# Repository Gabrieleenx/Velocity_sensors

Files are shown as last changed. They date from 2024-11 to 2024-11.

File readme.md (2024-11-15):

# Velocity sensor 

This is a build guide for the velocity sensor used in the paper "Perception, Control and Hardware for In-Hand Slip-Aware Object Manipulation with Parallel Grippers", preprint available at: https://arxiv.org/abs/2410.19660. Everything is provided as is. 

The main repo for that project can be found at https://github.com/Gabrieleenx/Slip-Aware-Object-Manipulation-with-Parallel-Grippers 

This readme contains the following:
* Overview
* Overview of code
* Parts list
* Build guide

## Overview 

This repo is about the velocity sensors that are mounted on the figers of the gripper described in https://github.com/Gabrieleenx/Slip-Aware-Object-Manipulation-with-Parallel-Grippers. I have plans to redesign these sensors, the current version funciton and does what they where built to do, but there are some properties I would like to improve. The sensors can be seen bellow:

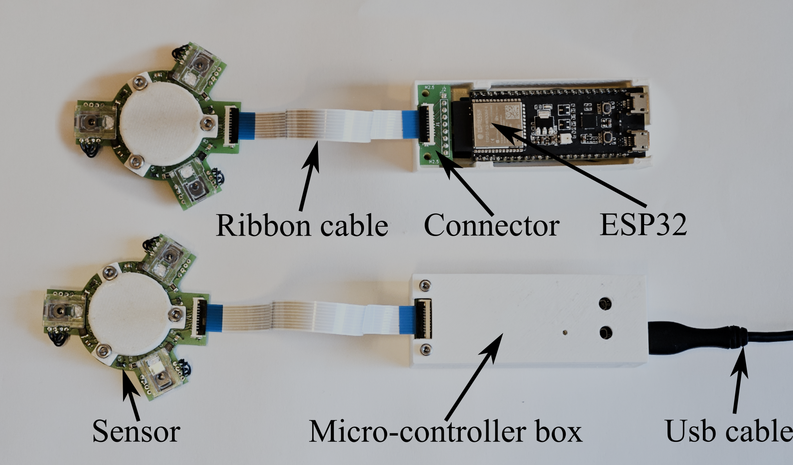
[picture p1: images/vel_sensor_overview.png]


These senors are mounted on the gripper like following:

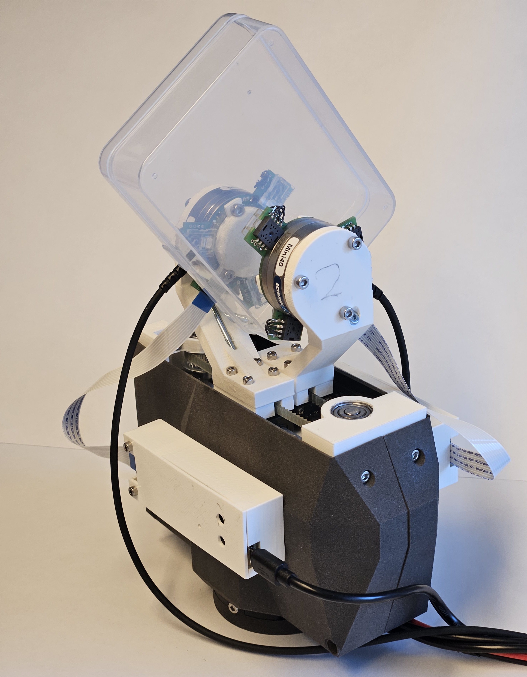
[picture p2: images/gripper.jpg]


The sensor can meassure velocity in x, y and rotation for a flat surface sliding in the gripper. Currently I have the sensor output velocity measurements at 120 Hz. And they have simple outlier rejection, where if one sensor is outside of the object, the tracking still functions. 

## Overview of code

The code can be found in the folder /code. The code is compiled using platfromIO, see the platformio.ini for the settings. 

One important thing is to set the "sensor_name = "sensor_2";" variable on line 16 in main.cpp, to either "sensor_1" or "sensor_2" depending on which finger it goes on, you can make up your own names aswell. 

The code to communicate with the sensors can be found at  https://github.com/Gabrieleenx/Slip-Aware-Object-Manipulation-with-Parallel-Grippers.

The code uses freeRTOS, built into the Arduio framework, one core is tasked with bitbanging the sensors and the other is doing filtering and serial communication. Here we use the ESP32-S3-DEVKITC-1-N8R2, whcih has the UART to USB, in comparion to the gripper, https://github.com/Gabrieleenx/Parallel_gripper. 

## Parts list

This part list is for one sensor:

1x ESP32-S3-DEVKITC-1-N8R2 https://www.digikey.se/sv/products/detail/espressif-systems/ESP32-S3-DEVKITC-1-N8R2/15199627?productid=15199627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

3x rapoo m300 (we will take the chip, lens and LED) https://www.rapoo-eu.com/product/m300-silent/

3x 50 ohm resisor https://se.rs-online.com/web/p/surface-mount-resistors/2430511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

1x hrough Hole Pin Header https://se.rs-online.com/web/p/pcb-headers/7671025?searchId=941cb68f-9620-4753-9d9d-7a9d76368953&gb=s

2x Molex, Easy-On, 200528 1mm Pitch 9, https://se.rs-online.com/web/p/fpc-connectors/1213341?searchId=74c22de1-7fd5-41bc-b195-446cd1a22052&gb=s

1x FFC Ribbon Cable, 9-Way, 1mm Pitch, 152mm, https://se.rs-online.com/web/p/ribbon-cable/1222519?searchId=01f7c47b-5acd-4eca-bbf9-52f6bdeb05a2&gb=s 

3x 10μF Tantalum Capacitor 16V dc, https://se.rs-online.com/web/p/tantalum-capacitors/1882267?searchId=6749729e-8b06-4c40-b989-853f3fd36829&gb=s

3x 1μF Tantalum Capacitor 16V dc, https://se.rs-online.com/web/p/tantalum-capacitors/1882297?searchId=ff8f216c-4b23-46ba-a96b-6da0473a7bb6&gb=s

3x 100nF Multilayer Ceramic Capacitor MLCC, https://se.rs-online.com/web/p/mlccs-multilayer-ceramic-capacitors/2644416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

1x USB cable, with micro usb

dupont cables

2x m2.5 20mm screw and nut to mount the lid

2x m2.5 srew and nut to mount the microcontroller box, length depends on

3x m3 screw, to mount the sensor, length depends on

## PCB boards
* Sensor board 2 layer, see gerber files (traces have been updated, jumper wires no longer needed)
* Connector board 2 layer, see gerber files 

## 3D print

The controleller box is printed in 2 pices, bottom and top, both in PLA. The contact pad stl can be found at https://github.com/Gabrieleenx/Parallel_gripper. Otherwise see stl_files.

## Build guide

See below for how to solder on the componenets or chech the gerberfiles. The same pattern follows for all 3 sensors. 

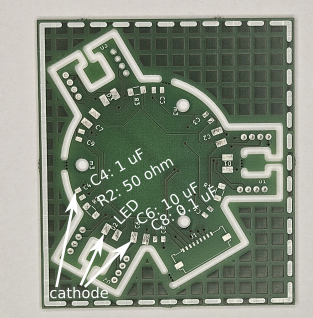
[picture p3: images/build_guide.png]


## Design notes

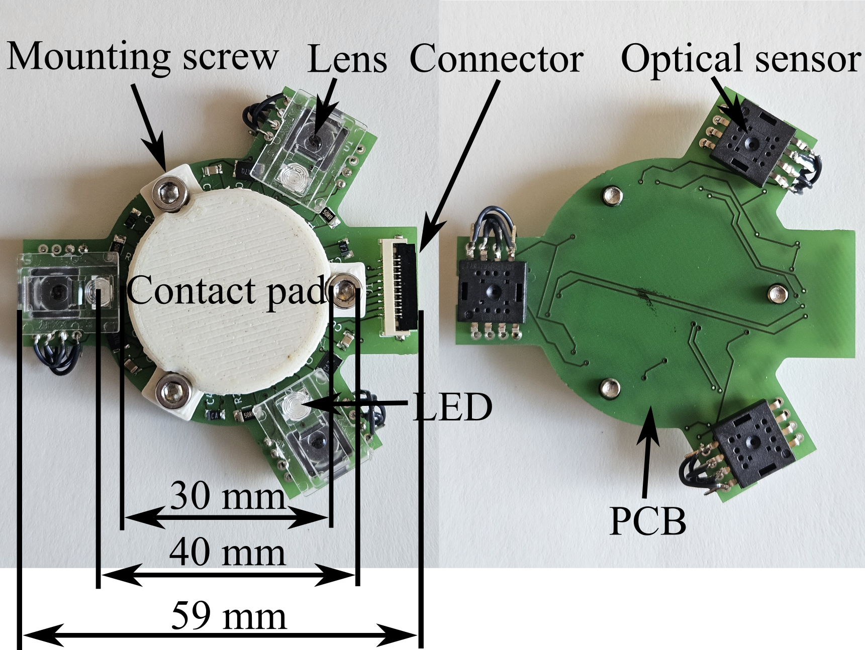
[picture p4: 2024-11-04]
images/vel_sensors.png

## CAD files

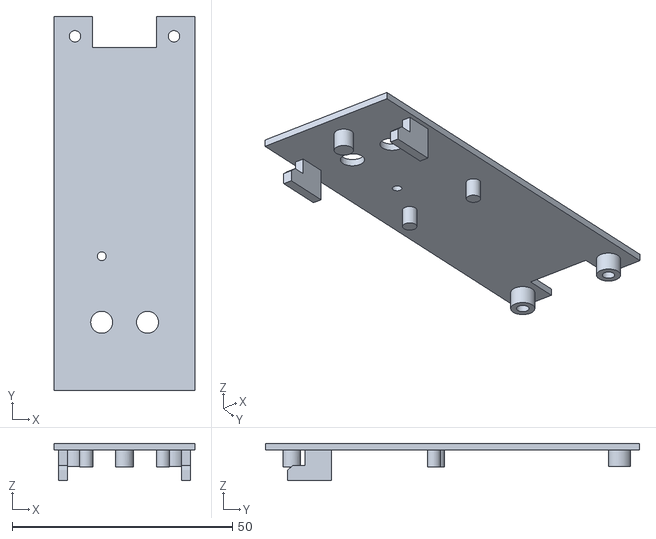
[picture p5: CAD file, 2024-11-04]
stl_files/Hull_top.stl
32.0 x 85.0 x 8.50

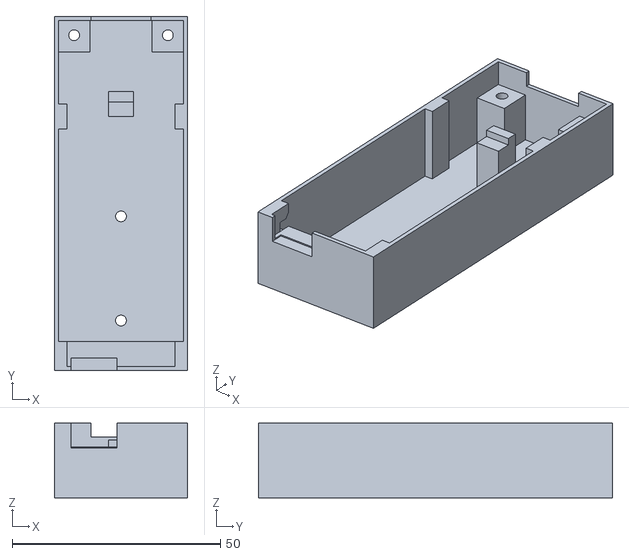
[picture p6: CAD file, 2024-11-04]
stl_files/Hull_bottom.stl
32.0 x 85.0 x 18.0

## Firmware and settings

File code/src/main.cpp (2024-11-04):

#include <Arduino.h>
#include "esp_task_wdt.h"
#include "FreeRTOS.h"
#include "task.h"
#include <EEPROM.h>
#include "filter_utils.h"
const int data_pin_sensor_1 = 4;
const int clk_pin_sensor_1 = 5;

const int data_pin_sensor_2 = 6;
const int clk_pin_sensor_2 = 7;

const int data_pin_sensor_3 = 15;
const int clk_pin_sensor_3 = 16;

const String sensor_name = "sensor_2";

int counts_per_inch = 3200; // should be 1600, but measurements say otherwise. sensor resulution.

const double d = 0.026; // [m] from center to sensor. 

int correct_prod_id1 = 0x31; // ID of sensor 

int individual_sensor = 0;

const uint8_t sensor_reg_dx = 0x03; // 0x03
const uint8_t sensor_reg_dy = 0x04; // 0x04
const uint8_t sensor_reg_motion = 0x02;
const uint8_t sensor_reg_PId1 =0x00;
unsigned long lastTimeMicros_;

const double tracking_loop_Kp = 40;
const double tracking_loop_Ki = 500;

bool connected_sensor_1 = 0;
bool connected_sensor_2 = 0;
bool connected_sensor_3 = 0;

// FreeRTOS handles for the tasks and mutex
TaskHandle_t sensorTaskHandle;
TaskHandle_t serialTaskHandle;
SemaphoreHandle_t mutex;

// Global data storage


SensorDataDelta sensor_1_delta = {0, 0};
SensorDataDelta sensor_2_delta = {0, 0};
SensorDataDelta sensor_3_delta = {0, 0};

// Useful functions

void setAllDataInput(){
  pinMode (data_pin_sensor_1, INPUT); 
  pinMode (data_pin_sensor_2, INPUT); 
  pinMode (data_pin_sensor_3, INPUT); 
}

void setAllDataOutput(){
  pinMode (data_pin_sensor_1, OUTPUT); 
  pinMode (data_pin_sensor_2, OUTPUT); 
  pinMode (data_pin_sensor_3, OUTPUT); 
}


void setAllClkOutput(){
  pinMode (clk_pin_sensor_1, OUTPUT); 
  pinMode (clk_pin_sensor_2, OUTPUT); 
  pinMode (clk_pin_sensor_3, OUTPUT); 
}

void digitalWriteDataAll(int w){
 
  digitalWrite(data_pin_sensor_3, w);
  digitalWrite(data_pin_sensor_2, w);
  digitalWrite(data_pin_sensor_1, w);
          
}

void digitalWriteClkAll(int w){
  digitalWrite(clk_pin_sensor_1, w);
  digitalWrite(clk_pin_sensor_3, w); 
  digitalWrite(clk_pin_sensor_2, w);  
}



void sensorWriteReg(uint8_t address, uint8_t data){
  // Set MSB high
  address |= 0x80;
  setAllDataOutput();
  int t_hold = 5;
  for (int i=7; i>=0; i--){
    digitalWriteClkAll(LOW);
    digitalWriteDataAll(address & (1 << i));
    delayMicroseconds(t_hold);
    digitalWriteClkAll(HIGH);
    delayMicroseconds(t_hold);
  }
  for (int i=7; i>=0; i--){
    digitalWriteClkAll(LOW);
    digitalWriteDataAll(data & (1 << i));
    delayMicroseconds(t_hold);
    digitalWriteClkAll(HIGH);
    delayMicroseconds(t_hold);
  }
}

void sensorReadReg(const uint8_t address, int* r){
  setAllDataOutput();
  int t_hold = 5;

  for (int i=7; i>=0; i--){
    digitalWriteClkAll(LOW);
    digitalWriteDataAll(address & (1 << i));
    delayMicroseconds(t_hold);
    digitalWriteClkAll(HIGH);
    delayMicroseconds(t_hold);
  }

  digitalWriteDataAll(LOW); 
  delayMicroseconds(2);
  setAllDataInput();
  delayMicroseconds(2);
  
  for (int i=7; i>=0; i--){        
    digitalWriteClkAll(LOW);
    delayMicroseconds(t_hold);
    digitalWriteClkAll(HIGH);
    delayMicroseconds(t_hold);
    
    r[2] |= (digitalRead(data_pin_sensor_3) << i);
    r[1] |= (digitalRead(data_pin_sensor_2) << i);
    r[0] |= (digitalRead(data_pin_sensor_1) << i);
    
  }

}


void reSynchSensor(){
  // This assumes same procedure as PAW3204 
  setAllDataOutput();
  digitalWriteDataAll(LOW);
  setAllDataInput(); // set in HI-Z
  digitalWriteClkAll(HIGH);
  delayMicroseconds(5);
  digitalWriteClkAll(LOW); 
  delayMicroseconds(2);
  digitalWriteClkAll(HIGH); 
  delay(5); // t_siwtt, timeout watchdog 1.7 ms
  sensorWriteReg(0x85, 0x21); // reg: 85 data: 0x21   00100001 write operation mode    force wake up with disabled sleep
  sensorWriteReg(0x86, 0x06); // 86 06   write configuration      CPI 1600  // 00000110
}


void getProdID(signed char* prod_id){
  int r[3] = {0,0,0};
  sensorReadReg(sensor_reg_PId1, r);
  prod_id[0] = (signed char) r[0];
  prod_id[1] = (signed char) r[1];
  prod_id[2] = (signed char) r[2];
}


void sensorDx(signed char* dx){
  int r[3] = {0,0,0};
  sensorReadReg(sensor_reg_dx, r);
  dx[0] = (signed char) r[0];
  dx[1] = (signed char) r[1];
  dx[2] = (signed char) r[2];
} 

void sensorDy(signed char* dy){
  int r[3] = {0,0,0};
  sensorReadReg(sensor_reg_dy, r);
  dy[0] = (signed char) r[0];
  dy[1] = (signed char) r[1];
  dy[2] = (signed char) r[2];
} 

int extractBit7(int value) {
  return (value >> 7) & 1;
}

void sensorMotion(int* motion){
  int r[3] = {0,0,0};
  sensorReadReg(sensor_reg_motion, r);
  motion[0] = extractBit7(r[0]);
  motion[1] = extractBit7(r[1]);  
  motion[2] = extractBit7(r[2]);
}

void setSensorSettings(){
  // set up 3 sensors
  int i = 0;
  signed char sensor_prod_id[] = {0,0,0};

  while(i < 100){
    reSynchSensor();
    getProdID(sensor_prod_id);
    if (sensor_prod_id[0] == correct_prod_id1){
      connected_sensor_1 = 1;
    }
    else{
      Serial.print("Chip 1 prodid");
      Serial.println(sensor_prod_id[0]);   
    }
    if (sensor_prod_id[1] == correct_prod_id1){
      connected_sensor_2 = 1;
    }
    else{
      Serial.print("Chip 2 prodid");
      Serial.println(sensor_prod_id[1]);   
    }
    if (sensor_prod_id[2] == correct_prod_id1){
      connected_sensor_3 = 1;
    }    else{
      Serial.print("Chip 3 prodid");
      Serial.println(sensor_prod_id[2]);   
    }

    if (connected_sensor_1 == 1 && connected_sensor_2 == 1 && connected_sensor_3 == 1){
      break;
    }
    i++;
    delay(1);
  }
  sensorWriteReg(0x85, 0x21); // reg: 85 data: 0x21   00100001 write operation mode    force wake up with disabled sleep
  sensorWriteReg(0x86, 0x86); // chip reset 
  delayMicroseconds(3); 
  sensorWriteReg(0x85, 0x21); // reg: 85 data: 0x21   00100001 write operation mode    force wake up with disabled sleep
  sensorWriteReg(0x86, 0x06); // 86 06   write configuration      CPI 1600  // 00000110
}

void readSerial(String& msg, FilterSensorData &sensor_filter){
  while (Serial.available()) {
    // get the new byte:
    char ch = Serial.read();
    msg += ch;
    // end of user input
    if (ch == '\n') {
      if (msg[0] == 'n'){
      // send name of sensor 
      Serial.print("n");
      Serial.print("/t");
      Serial.println(sensor_name); 
      }
      if (msg[0] == 'c'){
        individual_sensor = msg[1] - '0';
      }
      if (msg[0] == 'k'){
        /* 
        cal_nr = {0,x: radious, 1,0: s_1_x_a, 1,1: s_1_x_b,
                  1,2: s_1_y_a, 1,3: s_1_y_b,
                  2,0: s_2_x_a, 2,1: s_2_x_b,
                  2,2: s_2_y_a, 2,3: s_2_y_b,
                  3,0: s_3_x_a, 3,1: s_3_x_b,
                  3,2: s_3_y_a, 3,3: s_3_y_b,}
        */
        int cal_nr_1 = msg[1] - '0';
        int cal_nr_2 = msg[2] - '0';
        String substr = msg.substring(3);

        double value = substr.toDouble();
        sensor_filter.update_calibration(cal_nr_1, cal_nr_2, value);
      }
      msg = "";
      return;
    }
  }
}



void sensorUpdate(){
  signed char dx[] = {0,0,0};
  signed char dy[] = {0,0,0};
  int motion[] = {0,0,0};

  // check that sensor is in sync by reading the sensor id
  signed char sensor_prod_id[] = {0,0,0};
  getProdID(sensor_prod_id);
  if (sensor_prod_id[0] == correct_prod_id1 && sensor_prod_id[1] == correct_prod_id1 && sensor_prod_id[2] == correct_prod_id1){
    
    sensorMotion(motion);

    sensorDy(dy);
    sensorDx(dx);
    if( xSemaphoreTake( mutex, ( TickType_t ) 10 ) == pdTRUE ){
      sensor_1_delta.dx += (int) dx[0];
      sensor_1_delta.dy += (int) dy[0];

      sensor_2_delta.dx += (int) dx[1];
      sensor_2_delta.dy += (int) dy[1];

      sensor_3_delta.dx += (int) dx[2];
      sensor_3_delta.dy += (int) dy[2];
      xSemaphoreGive( mutex );
    }
    vTaskDelay(1);

  }
  else{
    Serial.print("n");
    Serial.print("/t");
    Serial.println("resynch");
    Serial.print(sensor_prod_id[0]);
    Serial.print(" ");
    Serial.print(sensor_prod_id[1]);
    Serial.print(" ");
    Serial.println(sensor_prod_id[2]);
    reSynchSensor();
    return;
  }
}


void sensorLoop(void *pvParameters) {
  setSensorSettings();
  while (true) {
    sensorUpdate();
  }
}


void serialTask(void *pvParameters) {
  SensorDataDelta sensor_1_delta_copy = {0, 0};
  SensorDataDelta sensor_2_delta_copy = {0, 0};
  SensorDataDelta sensor_3_delta_copy = {0, 0};
  FilterSensorData sensor_filter(80, 300, counts_per_inch);
  String msg = "";
  while (true) {

    if( xSemaphoreTake( mutex, ( TickType_t ) 10 ) == pdTRUE ){
      sensor_1_delta_copy = sensor_1_delta;
      sensor_1_delta.reset();
      sensor_2_delta_copy = sensor_2_delta;
      sensor_2_delta.reset();
      sensor_3_delta_copy = sensor_3_delta;
      sensor_3_delta.reset();
      xSemaphoreGive( mutex );
    }
    if (individual_sensor == 0){
      sensor_filter.update(sensor_1_delta_copy, sensor_2_delta_copy, sensor_3_delta_copy);
      Serial.print("v");
      Serial.print("/t");
      Serial.print(sensor_filter.get_vx(), 4);
      Serial.print("/t");
      Serial.print(sensor_filter.get_vy(), 4);
      Serial.print("/t");
      Serial.println(sensor_filter.get_omega(), 4);
    }
    else{
      unsigned long currentTimeMicros = micros(); 
      // Overflows after 71.58 min
      if (currentTimeMicros < lastTimeMicros_){
        lastTimeMicros_ = currentTimeMicros;
      }
      double dt =  ((double)(currentTimeMicros - lastTimeMicros_))/1e6; 
      lastTimeMicros_ = currentTimeMicros;
      double vx = 0.0;
      double vy = 0.0;
      double omega = 0.0;
      if (individual_sensor == 1){
        vx = dxToMilimeter(sensor_1_delta_copy.dx, counts_per_inch)/dt;
        vy = dxToMilimeter(sensor_1_delta_copy.dy, counts_per_inch)/dt;
      }
      if (individual_sensor == 2){
        vx = dxToMilimeter(sensor_2_delta_copy.dx, counts_per_inch)/dt;
        vy = dxToMilimeter(sensor_2_delta_copy.dy, counts_per_inch)/dt;
      }
      if (individual_sensor == 3){
        vx = dxToMilimeter(sensor_3_delta_copy.dx, counts_per_inch)/dt;
        vy = dxToMilimeter(sensor_3_delta_copy.dy, counts_per_inch)/dt;
      }


      Serial.print("v");
      Serial.print("/t");
      Serial.print(vx, 4);
      Serial.print("/t");
      Serial.print(vy, 4);
      Serial.print("/t");
      Serial.println(sensor_filter.get_omega(), 4);

    }
   
    readSerial(msg, sensor_filter);
    vTaskDelay(6);
  }
}


void setup() {
  Serial.begin(115200);
  //Serial.println("Serial start");
  mutex = xSemaphoreCreateMutex();

  delay(10);

  // set pins 
  setAllClkOutput();
  setAllDataInput();

  //Serial.println("Begin setup");
  delay(1000);
  //Serial.println("Setup done");

  xTaskCreatePinnedToCore(
    sensorLoop,       // Task function
    "SensorTask",     // Name of the task
    2048,               // Stack size (bytes)
    NULL,               // Parameter to pass
    1,                  // Task priority
    &sensorTaskHandle,// Task handle
    0                   // Core to pin the task to (0 or 1)
  );
  
  xTaskCreatePinnedToCore(
    serialTask,       // Task function
    "SerialTask",     // Name of the task
    2048,               // Stack size (bytes)
    NULL,               // Parameter to pass
    1,                  // Task priority
    &serialTaskHandle, // Task handle
    1                   // Core to pin the task to (0 or 1)
  );
}

void loop() { 
// Do nothing 
}

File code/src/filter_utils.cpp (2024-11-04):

#include <Arduino.h>
#include "filter_utils.h"

double dxToMilimeter(int dx, int countsPerInch){
  double countsPerMilimeter = (double) countsPerInch / 25.4;
  double dx_mm = (double) dx/countsPerMilimeter;
  return dx_mm;
}


TargetTrackingLoopFilter::TargetTrackingLoopFilter(double kp_, double ki_, int countsPerInch_){
  //https://www.embeddedrelated.com/showarticle/530.php
  lastTimeMicros = micros();
  pos = 0.0;
  pos_est = 0.0;
  vel_est = 0.0;
  vel_int = 0.0;
  kp = kp_;
  ki = ki_;
  countsPerInch = countsPerInch_;
}

double TargetTrackingLoopFilter::update(int dx){
  // TOOD add calibration here 
  
  pos += dxToMilimeter(dx, countsPerInch);
  unsigned long currentTimeMicros = micros(); 
  // Overflows after 71.58 min
  if (currentTimeMicros < lastTimeMicros){
    lastTimeMicros = currentTimeMicros;
  }
  double dt =  ((double)(currentTimeMicros - lastTimeMicros))/1e6; 
  lastTimeMicros = currentTimeMicros;
  
  pos_est += vel_est*dt;
  double pos_error = pos - pos_est;
  vel_int += pos_error * ki * dt; 
  vel_est = pos_error*kp + vel_int;
  
  double vel_est_ = dxToMilimeter(dx, countsPerInch)/dt;
  return vel_est_;
}

VelocityFilter::VelocityFilter(double a_, double b_, int countsPerInch_){
  lastTimeMicros = micros();
  countsPerInch = countsPerInch_;
  a = a_;
  b = b_;
}

double VelocityFilter::update(int dx){
  unsigned long currentTimeMicros = micros(); 
  // Overflows after 71.58 min
  if (currentTimeMicros < lastTimeMicros){
    lastTimeMicros = currentTimeMicros;
  }
  double dt =  ((double)(currentTimeMicros - lastTimeMicros))/1e6; 
  lastTimeMicros = currentTimeMicros;

  double vel_est_ = dxToMilimeter(dx, countsPerInch)/dt;
  double cal_vel_est = vel_est_/(b + a*vel_est_);
  return cal_vel_est;
}


FilterSensorData::FilterSensorData(double kp_, double ki_, int countsPerInch_)
    : ttlf_dx_1(0.0, 1.0, countsPerInch_),
      ttlf_dy_1(0.0, 1.0, countsPerInch_),
      ttlf_dx_2(0.0, 1.0, countsPerInch_),
      ttlf_dy_2(0.0, 1.0, countsPerInch_),
      ttlf_dx_3(0.0, 1.0, countsPerInch_),
      ttlf_dy_3(0.0, 1.0, countsPerInch_) {
  d_Sensor = 20.3; // [mm] from center to sensor. 
}

void FilterSensorData::update_calibration(int cal_nr_1, int cal_nr_2, double value){
  if (cal_nr_1 == 0){
    d_Sensor = value;
    Serial.print("radius is updated to: ");
    Serial.println(d_Sensor);
    return;
  }
  if (cal_nr_1 == 1){
    if (cal_nr_2 == 0) {
      ttlf_dx_1.update_a(value);
      return;
    }
    if (cal_nr_2 == 1) {
      ttlf_dx_1.update_b(value);
      return;
    }
    if (cal_nr_2 == 2) {
      ttlf_dy_1.update_a(value);
      return;
    }
    if (cal_nr_2 == 3) {
      ttlf_dy_1.update_b(value);
      return;
    }
  }

  if (cal_nr_1 == 2){
    if (cal_nr_2 == 0) {
      ttlf_dx_2.update_a(value);
      return;
    }
    if (cal_nr_2 == 1) {
      ttlf_dx_2.update_b(value);
      return;
    }
    if (cal_nr_2 == 2) {
      ttlf_dy_2.update_a(value);
      return;
    }
    if (cal_nr_2 == 3) {
      ttlf_dy_2.update_b(value);
      return;
    }
  }

  if (cal_nr_1 == 3){
    if (cal_nr_2 == 0) {
      ttlf_dx_3.update_a(value);
      return;
    }
    if (cal_nr_2 == 1) {
      ttlf_dx_3.update_b(value);
      return;
    }
    if (cal_nr_2 == 2) {
      ttlf_dy_3.update_a(value);
      return;
    }
    if (cal_nr_2 == 3) {
      ttlf_dy_3.update_b(value);
      return;
    }
  }


}



void FilterSensorData::update(SensorDataDelta sensor_1, 
                              SensorDataDelta sensor_2, 
                              SensorDataDelta sensor_3){
  // Velocity tracking loop
  double vx_1 = ttlf_dx_1.update(sensor_1.dx);
  double vy_1 = ttlf_dy_1.update(sensor_1.dy);

  double vx_2 = ttlf_dx_2.update(sensor_2.dx);
  double vy_2 = ttlf_dy_2.update(sensor_2.dy);

  double vx_3 = ttlf_dx_3.update(sensor_3.dx);
  double vy_3 = ttlf_dy_3.update(sensor_3.dy);


  vx = sqrt(3.0)/6.0 * vx_1 - 1.0/6.0 * vy_1 - sqrt(3.0)/6.0 * vx_2 - 1.0/6.0 * vy_2 + 1.0/3.0 * vy_3;
  vy = -1.0/6.0 * vx_1 - sqrt(3.0)/6.0 * vy_1 - 1.0/6.0 * vx_2 + sqrt(3.0)/6.0 * vy_2 + 1.0/3.0 * vx_3;
  omega = 1.0/(3.0*d_Sensor) * (vx_1 + vx_2 + vx_3);

  // calculate error for each sensor 
  double vx_1_hat = cos(PI/6)*vx - sin(PI/6)*vy + d_Sensor*omega;
  double vy_1_hat = -sin(PI/6)*vx - cos(PI/6)*vy;
  double vx_2_hat = -cos(-PI/6)*vx + sin(-PI/6)*vy + d_Sensor*omega;
  double vy_2_hat = sin(-PI/6)*vx + cos(-PI/6)*vy;
  double vx_3_hat = vy + d_Sensor*omega;
  double vy_3_hat = vx;

  double e_1 = sqrt(pow(vx_1-vx_1_hat, 2) + pow(vy_1-vy_1_hat, 2));
  double e_2 = sqrt(pow(vx_2-vx_2_hat, 2) + pow(vy_2-vy_2_hat, 2));
  double e_3 = sqrt(pow(vx_3-vx_3_hat, 2) + pow(vy_3-vy_3_hat, 2));
  double e_t = sqrt(pow(e_1, 2) + pow(e_2, 2) + pow(e_3, 2));
  double v_1 = sqrt(pow(vx_1, 2) + pow(vy_1, 2)); 
  double v_2 = sqrt(pow(vx_2, 2) + pow(vy_2, 2));
  double v_3 = sqrt(pow(vx_3, 2) + pow(vy_3, 2));

  double v_t = sqrt(pow(v_1, 2) + pow(v_2, 2) + pow(v_3, 2));;

  double e_r = e_t/(v_t + 1);

  double e_treashold = 0.2;
  // Check if error ratio is too high, indicating that a sensor is not reading surface 
  if (e_r > e_treashold){
    // Assume that the sensor with lowest velocity is the incorrect one.
    // For example if a sensor is outside the object it would read 0 velocity. 
    if (v_1 < v_2 && v_1 < v_3){
        //Serial.println("Sensor 1");
        vx = - sqrt(3.0)/8.0 * vx_2 - 3.0/8.0 * vy_2 + sqrt(3.0)/8.0 * vx_3 + 5.0/8.0 * vy_3;
        vy =   -3.0/8.0 * vx_2 + 7*sqrt(3.0)/24.0 * vy_2 + 3.0/8.0 * vx_3 - sqrt(3.0)/24.0 * vy_3;
        omega = 1.0/(2.0*d_Sensor) * vx_2 -  sqrt(3.0)/(6.0*d_Sensor) * vy_2 + 1.0/(2.0*d_Sensor) * vx_3 + sqrt(3.0)/(6.0*d_Sensor) * vy_3;
    }
    if (v_2 < v_1 && v_2 < v_3){
        //Serial.println("Sensor 2");
        vx =  sqrt(3.0)/8.0 * vx_1 - 3.0/8.0 * vy_1 - sqrt(3.0)/8.0 * vx_3 + 5.0/8.0 * vy_3;
        vy =   -3.0/8.0 * vx_1 - 7*sqrt(3.0)/24.0 * vy_1 + 3.0/8.0 * vx_3 + sqrt(3.0)/24.0 * vy_3;
        omega = 1.0/(2.0*d_Sensor) * vx_1 +  sqrt(3.0)/(6.0*d_Sensor) * vy_1 + 1.0/(2.0*d_Sensor) * vx_3 - sqrt(3.0)/(6.0*d_Sensor) * vy_3;
    }
    if (v_3 < v_2 && v_3 < v_1){
        //Serial.println("Sensor 3");
        vx =  sqrt(3.0)/4.0 * vx_1 - 1.0/4.0 * vy_1 - sqrt(3.0)/4.0 * vx_2 - 1.0/4.0 * vy_2;
        vy =   - sqrt(3.0)/3.0 * vy_1 + sqrt(3.0)/3.0 * vy_2;
        omega = 1.0/(2.0*d_Sensor) * vx_1 -  sqrt(3.0)/(6.0*d_Sensor) * vy_1 + 1.0/(2.0*d_Sensor) * vx_2 + sqrt(3.0)/(6.0*d_Sensor) * vy_2;
    }
  }

}
